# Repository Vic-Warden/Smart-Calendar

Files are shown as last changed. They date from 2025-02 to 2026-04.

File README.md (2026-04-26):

# Field Command: Pattern Cuckoo

An IoT smart calendar system built around an **ESP32** microcontroller with a Warhammer 40K aesthetic. The device retrieves appointments from a web API, displays them on an LCD, plays audio cues via a DFPlayer Mini, and adapts to ambient light. The web interface features a static landing page and a Svelte SPA.

---

## Stack

| Layer | Technology |
|---|---|
| Embedded | ESP32, PIR sensor, LDR, servo, DFPlayer Mini, I2C LCD, TM1637 |
| Backend | PHP, MariaDB (MySQL) |
| Frontend | HTML, Tailwind CSS, Three.js, Svelte + Vite |
| Infrastructure | Docker (Nginx, PHP-FPM, MariaDB, phpMyAdmin, tunnel) |

---

## Requirements

- Docker & Docker Compose
- A `.env` file at the project root (see below)

---

## Setup

1. Create a `.env` file:

```env
WEBSERVER_PORT=80
MYSQL_PORT=3306
MYSQL_ROOT_PASSWORD=your_password
HVA_USERNAME=your_username
```

2. Start the stack:

```bash
docker-compose up -d
```

| Service | URL |
|---|---|
| Web app | http://localhost/ |
| Dashboard | http://localhost/dashboard |
| phpMyAdmin | http://localhost/phpmyadmin |

---

## Project Structure

```
├── docs/          # Portfolio documentation (MkDocs)
├── embedded/      # ESP32 source code (.ino)
├── web/           # PHP, HTML, CSS, JS, assets
├── omnissiah-info/# Svelte SPA (Vite)
├── docker/        # Docker images & config
└── docker-compose.yml
```

---

## Database

| Parameter | Value |
|---|---|
| Host (from PHP) | `mariadb` |
| Host (from host) | `localhost` |
| Port | `3306` |
| Username | `root` |
| Password | See `.env` |

> Create the database manually via phpMyAdmin or MySQL CLI before first use.

---

## Communication Overview

| Source | Destination | Protocol | Port |
|---|---|---|---|
| ESP32 | PHP API | HTTP | 80 |
| ESP32 | NTP Pool | UDP | 123 |
| Mobile/Browser | Nginx | HTTPS | 443 |
| Nginx | PHP-FPM | FastCGI | 9000 |
| PHP | MariaDB | MySQL | 3306 |
| Vite Dev Server | Browser | WebSocket | 5173 |

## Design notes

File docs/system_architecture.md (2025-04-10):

# System Architecture

This page describes the system architecture of the full project, including software, hardware, and their communication. It provides a clear overview of all components within the existing Docker environment.  

This document is regularly updated to reflect the current state of the project.

---

## Introduction  

This document outlines the system architecture of my project, Field Command: Pattern Cuckoo, presenting a structured overview of its components, including software, databases, and network elements. It explains how these components interact with each other.  
The described architecture includes all elements currently present in the Docker environment.  
Its primary purpose is to serve as a reference for understanding the system.

---

## Legend  

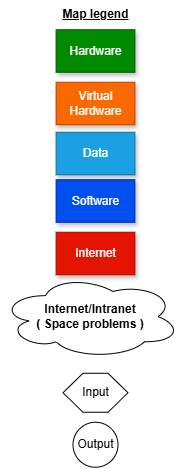
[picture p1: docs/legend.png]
  

---

## SAD#01, SAD#02, and SAD#03  

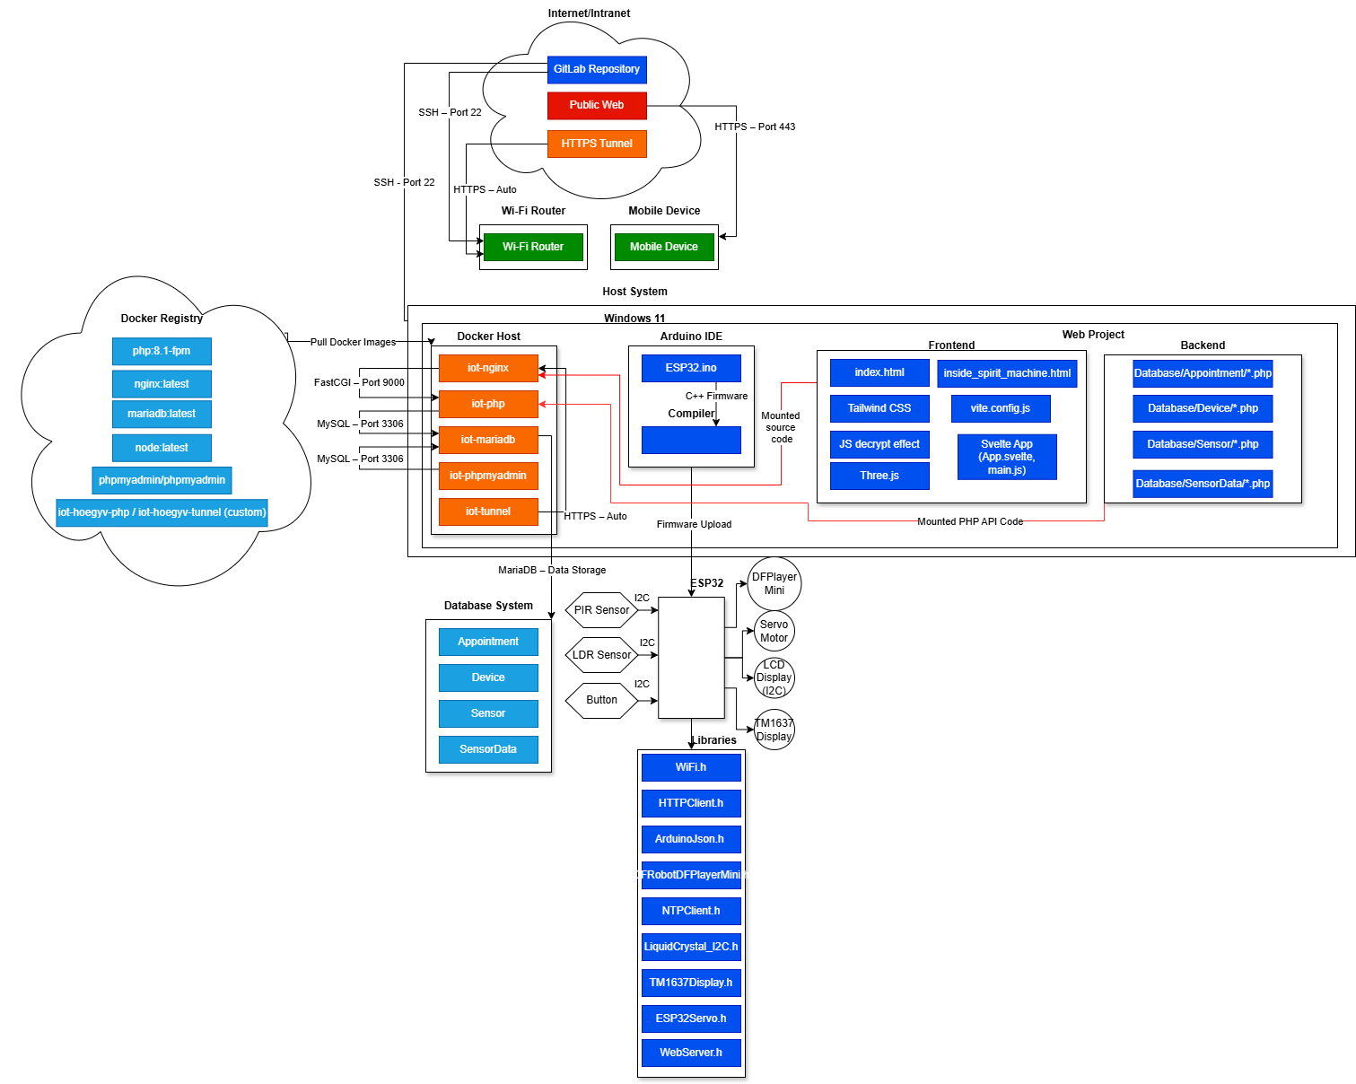
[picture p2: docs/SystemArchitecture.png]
  

---

## SAD#04  

| Source | Destination | Protocol | Port | Description |
|---|---|---|---|---|
| ESP32 | PHP API | HTTP | 80 | Retrieves + sends sensor data |
| ESP32 | NTP Pool | UDP | 123  | Time synchronization |
| ESP32 | Internal Web Server| HTTP | 80 | Testing / character switching |
| Mobile Device  | iot-nginx | HTTPS | 443  | User interface |
| iot-nginx | iot-php | FastCGI  | 9000 | API Proxy |
| iot-php | iot-mariadb | MySQL | 3306 | SQL Queries |
| phpmyadmin | iot-mariadb | MySQL | 3306 | DB Administration |
| Vite DevServer | Web Browser | WebSocket| 5173 | Live reload / frontend development |
| iot-tunnel | Internet | HTTPS | auto | Public exposure of the project |
| Host | GitLab | SSH | 22 | Code Push/Pull |

---

## SAD#05  

Menu 

---

## SAD#06  

### Hardware Components  

- **ESP32**  
- **Sensors**: PIR (motion), LDR (light), button  
- **Actuators**: Servo motor, DFPlayer Mini (audio)  
- **I2C LCD Display (16x2)**  
- **7-segment TM1637 display**  

**ESP32 Software**  

**Libraries Used**  

| Library | Role |
|---|---|
| WiFi.h | Connects ESP32 to Wi-Fi network |
| HTTPClient.h | HTTP communication with PHP APIs |
| ArduinoJson.h | Processes JSON data sent/received from the API |
| DFRobotDFPlayerMini.h | Controls DFPlayer module for audio playback |
| NTPClient.h + WiFiUdp.h| Time synchronization via NTP protocol |
| LiquidCrystal_I2C.h | Manages LCD display (text, system status) |
| TM1637Display.h | Displays time on 7-segment display |
| ESP32Servo.h | Smooth servo motor control |
| WebServer.h | Built-in HTTP server (port 80) for local commands (e.g., switching) |

**Main Functions**  

- Retrieves appointments via API and displays them on the LCD  
- Sends sensor data to the database via HTTP  
- Plays sounds via DFPlayer based on events or time  
- Automatically switches to night mode based on ambient light  

---

## SAD#07  

## Static Frontend (HTML Pages) 

- index.html, inside_spirit_machine.html  
- CSS: Tailwind  
- JS: Interactions, decrypt effect  
- Three.js + STLLoader for 3D models  

## Dynamic Frontend (Svelte SPA)  

- App.svelte, main.js (Svelte)  
- vite.config.js (dev server)  
- style.css, index.html (entry point)  
- DevServer: Vite (port 5173)  

**Backend**  

**REST APIs located in /web/Database/**  

**/Connection/**

- database_connection.php

**/Appointment/** 

- insert_appointment.php  
- update_appointment.php  
- delete_appointment.php 
- recover_appointment.php

**/Device/**  

- insert_device.php  
- delete_device.php  
- recover_device.php 

**/Sensor/**  

- insert_sensor.php  
- delete_sensor.php
- recover_sensor.php  

**/SensorData/**  

- insert_sensor_data.php
- recover_sensor_data.php  

---

## SAD#08  

- Container: iot-mariadb  
- Databases: iot, mysql, performance_schema  
- Tables: Appointment, Device, Sensor, SensorData  

---

## SAD#09  

- iot-hoegyv-php, iot-hoegyv-tunnel (custom images)  
- nginx:latest, mariadb:latest, phpmyadmin/phpmyadmin  

---

## SAD#10  

Containers running in the iot_default network:  
- iot-nginx: Web server (port 80)  
- iot-php: PHP-FPM backend  
- iot-mariadb: MariaDB database (port 3306)  
- iot-phpmyadmin: DB admin interface  
- iot-tunnel: SSH/HTTP tunnel for public exposure  

---

## SAD#11  

- Personal computer ASUS ROG Strix
- Operating system Windows 11
- Installed tools: Docker Engine, Git, IDE, browser  

---

## SAD#12  

- Android  
- Mobile OS + Chrome/Safari browser  
- Frontend interface access via HTTPS  

---

## SAD#13  

- Wi-Fi box or router  
- Connects all devices to the local network + Internet  

---

## SAD#14  

- Remote GitLab  
- .gitlab-ci.yml, .gitmodules  
- Uses SSH for push/pull  

---

## SAD#15  

- GitLab via HTTPS/SSH (port 22)  
- Public web access via iot-nginx  
- Tunnel via iot-tunnel  

---

## SAD#16  

- Container: iot-tunnel  
- Image: iot-hoegyv-tunnel  
- Public project exposure via HTTP/HTTPS tunnel  

---

**Last updated: April 7, 2025**

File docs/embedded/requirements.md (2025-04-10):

# 📜 Requirements

To build your embedded device, you need to have a clear idea of the requirements. On this page, you can describe the requirements of your embedded device. This includes the requirements from DLO, but also your own requirements.

Add some images! 😉

| Requirement ID# | Requirement | MoSCoW | Compliant |
|---|---|---|---|
| EMBRQ#01 | The embedded device acts as a client and sends measured sensor data to the application backend over http or https. | MUST | YES |
| EMBRQ#02 | The embedded device also acts as a server and receives status messages from the application backend over http or https. | MUST | YES |
| EMBRQ#03 | The embedded device contains at least two types of input sensors (e.g. LDR, buttons, joystick, capacitive touch, etc.). | MUST | YES |
| EMBRQ#04 | The embedded device contains at least two types of visual and/or sensory outputs (e.g. LED, LED Matrix, 7-segment display, motor, servo, etc.). | MUST | YES |
| EMBRQ#05 | The embedded device uses the WifiManager for configuration of SSID and password (PWD) for connecting to the network. | MUST | YES |

## EMBRQ#01

When a sensor (button, PIR or LDR) is triggered, it sends its data via a POST request, thanks to the HTTPClient library.
The API URL is defined in SENSOR_API_URL, and the sendSensorData function sends to the backend as long as WiFi is connected.

```c++

#include <WiFiManager.h>
#include <HTTPClient.h>

// The rest of the includes...

const char* SENSOR_API_URL = "http://100.74.252.69/Database/SensorData/insert_sensor_data.php";
const int DEVICE_ID = 1;

// The rest of the constants...

// Sends sensor data to the API server
 void sendSensorData(int sensor_id, float value) 
 {
   // Only send if WiFi is connected
   if (WiFi.status() != WL_CONNECTED) return;
 
   HTTPClient http;
   http.begin(SENSOR_API_URL);
   
   // Format POST data with all sensor values
   String postData = "device_id=" + String(DEVICE_ID) +
                    "&time_stamp=" + getCurrentTime() +
                    "&sensor_id_1=1&value_1=" + (sensor_id == BUTTON_SENSOR_ID ? String(value) : "0.0") +
                    "&sensor_id_2=2&value_2=" + (sensor_id == PIR_SENSOR_ID ? String(value) : "0.0") +
                    "&sensor_id_3=3&value_3=" + (sensor_id == LDR_SENSOR_ID ? String(value) : "0.0");
   
   http.POST(postData);
   http.end();
 }

// The rest of the functions...
```

## EMBRQ#02

I've defined several endpoints accessible via GET requests:

/ : returns a status message.

/appointments: returns appointments in JSON format.

/switch_character : changes character and triggers the voice of the selected character.

/play_random : plays a random sound.

The server is started in setupServer, enabling the backend to send instructions and receive data.

```c++

#include <WebServer.h>

// The rest of the includes...

WebServer server(80);
const char* SERVER_ROOT_RESPONSE = "Smart Calendar is online!";
const char* CONTENT_TYPE_TEXT = "text/plain";
const char* CONTENT_TYPE_JSON = "application/json";
const int HTTP_OK_CODE = 200;
const int HTTP_SERVICE_UNAVAILABLE_CODE = 503;

// The rest of the constants...

// Sets up the web server with all required endpoints
 void setupServer() 
 {
   // Root endpoint simple status response
   server.on("/", HTTP_GET, []() 
   {
     server.send(HTTP_OK_CODE, CONTENT_TYPE_TEXT, SERVER_ROOT_RESPONSE);
   });
 
   // Appointments endpoint returns current appointments as JSON
   server.on("/appointments", HTTP_GET, []() 
   {
     String json;
     serializeJson(appointments, json);
     server.send(HTTP_OK_CODE, CONTENT_TYPE_JSON, json);
   });
 
   // Character switch endpoint cycles to next character mode
   server.on("/switch_character", HTTP_GET, []() 
   {
     currentCharacter = static_cast<CharacterMode>((currentCharacter + 1) % CHARACTER_MODE_COUNT);
     String currentCharacterName = currentCharacterNames[currentCharacter];
 
     // Update display and play sound (if not in night mode)
     updateDisplay(LCD_MSG_SWITCHED, currentCharacterName, SHOWING_CHARACTER_NOTIFICATION);
     if (dfPlayerInitialized && !nightMode) 
     {
       switch (currentCharacter) 
       {
         case COMMISSAR: dfPlayer.play(COMMISSAR_TRACK); break;
         case LEMAN_RUSS: dfPlayer.play(LEMAN_RUSS_TRACK); break;
         case BANEBLADE: dfPlayer.play(BANEBLADE_TRACK); break;
       }
     }
 
     // Set notification timer
     showingCharacterNotification = true;
     characterNotificationStart = millis();
 
     // Return success response
     server.send(HTTP_OK_CODE, CONTENT_TYPE_TEXT, SERVER_SWITCH_RESPONSE + currentCharacterName);
   });
 
   // Play random endpoint plays random voice line for current character
   server.on("/play_random", HTTP_GET, []() 
   {
     if (dfPlayerInitialized && !nightMode) 
     {
       // Play random sound based on current character
       switch (currentCharacter) 
       {
         case COMMISSAR:
           playRandomSound(COMMISSAR_ACTIVE_TRACKS, sizeof(COMMISSAR_ACTIVE_TRACKS)/sizeof(int));
           break;
         case LEMAN_RUSS:
           playRandomSound(LEMAN_RUSS_ACTIVE_TRACKS, sizeof(LEMAN_RUSS_ACTIVE_TRACKS)/sizeof(int));
           break;
         case BANEBLADE:
           playRandomSound(BANEBLADE_ACTIVE_TRACKS, sizeof(BANEBLADE_ACTIVE_TRACKS)/sizeof(int));
           break;
       }

       server.send(HTTP_OK_CODE, CONTENT_TYPE_TEXT, "Random voice line played.");
     } 
     
     else 
     {
       // Return error if conditions not met
       server.send(HTTP_SERVICE_UNAVAILABLE_CODE, CONTENT_TYPE_TEXT, "Night mode active or DFPlayer unavailable.");
     }
   });
 
   server.begin();
   Serial.println(SERIAL_MSG_HTTP_STARTED);
 }

// The rest of the functions...
```

## EMBRQ#03

I use 3 inputs

A push-button (pin 14) used to change character.

A PIR sensor (pin 35) to detect movement.

An LDR sensor (pin 34) which measures ambient brightness.

All these sensors are read by the handleSensors function, and each change triggers an action ( sending data, sound ). 

```c++

#include <Wire.h>     
#include <ArduinoJson.h> 

// The rest of the includes...

 // Input 
 const int BUTTON_PIN = 14;             
 const int PIR_PIN = 35;                
 const int LDR_PIN = 34;

  enum SensorIds 
 {
   BUTTON_SENSOR_ID = 1, 
   PIR_SENSOR_ID = 2,        
   LDR_SENSOR_ID = 3           
 };

// The rest of the constants...

// Checks and handles sensor inputs
 void handleSensors(unsigned long currentMillis) 
 {
   // Only check sensors at defined interval
   if (currentMillis - lastSensorCheck >= SENSOR_CHECK_INTERVAL_MS) 
   {
     lastSensorCheck = currentMillis;
     
     // Read all sensor values
     int buttonState = digitalRead(BUTTON_PIN);
     int pirState = digitalRead(PIR_PIN);
     int ldrValue = analogRead(LDR_PIN);
     static bool wasInNightMode = nightMode;
     
     // Check for night mode transition
     bool newNightMode = (ldrValue < NIGHT_MODE_ENTER_THRESHOLD);
     if (newNightMode != nightMode) 
     {
       nightMode = newNightMode;
 
       // Play appropriate day/night sound if DFPlayer is ready
       if (dfPlayerInitialized) 
       {
         dfPlayer.play(nightMode ? DARK_TRACK : LIGHT_TRACK);
       }
 
       wasInNightMode = nightMode;
       sendSensorData(LDR_SENSOR_ID, ldrValue);
     }
 
     // Check for button press (with debouncing)
     if (buttonState == LOW && lastButtonState == HIGH && (currentMillis - lastButtonPress) >= BUTTON_DEBOUNCE_TIME_MS) 
     {
       sendSensorData(BUTTON_SENSOR_ID, VALUE_TRUE);
       
       // Cycle to next character mode
       currentCharacter = static_cast<CharacterMode>((currentCharacter + 1) % CHARACTER_MODE_COUNT);
       String currentCharacterName = currentCharacterNames[currentCharacter];
       
       // Show character switch notification
       updateDisplay(LCD_MSG_SWITCHED, currentCharacterName, SHOWING_CHARACTER_NOTIFICATION);
       
       // Play character-specific sound if not in night mode
       if (dfPlayerInitialized && !nightMode) 
       {
         switch(currentCharacter) 
         {
            case COMMISSAR: dfPlayer.play(COMMISSAR_TRACK); break;
            case LEMAN_RUSS: dfPlayer.play(LEMAN_RUSS_TRACK); break;
            case BANEBLADE: dfPlayer.play(BANEBLADE_TRACK); break;
         }
       }
       
       // Set notification display timer
       showingCharacterNotification = true;
       characterNotificationStart = currentMillis;
       lastButtonPress = currentMillis;
     }
 
     // Check for motion detection (with cooldown period )
     if (pirState == HIGH && lastPIRState == LOW && !pirLocked) 
     {
       sendSensorData(PIR_SENSOR_ID, VALUE_TRUE);
       
       // Play random motion sound if not in night mode
       if (dfPlayerInitialized && !nightMode) 
       {
         playRandomSound(PIR_TRACKS, sizeof(PIR_TRACKS)/sizeof(int));
       }
 
       // Start cooldown period
       lastPIRTime = currentMillis;
       pirLocked = true;
     }
 
     // Reset PIR lock after cooldown period
     if (pirLocked && currentMillis - lastPIRTime >= PIR_INTERVAL_MS) 
     {
       pirLocked = false;
     }
 
     // Update previous sensor states
     lastButtonState = buttonState;
     lastPIRState = pirState;
     lastLDRValue = ldrValue;
   }
 }

 // The rest of the functions...
```

## EMBRQ#04

I use 4 outputs

LCD display (I2C): displays appointments and system messages via updateDisplay

7-segment display: displays time in real time via update7SegmentDisplay.

DFPlayer audio module: plays sounds in response to events (sensors, changes) via playRandomSound

Servomotor: performs a movement every hour via handleHourlyServo

```c++

#include <LiquidCrystal_I2C.h>   
#include <TM1637Display.h>       
#include <DFRobotDFPlayerMini.h> 
#include <ESP32Servo.h>       

// The rest of the includes...

// LCD
 const int LCD_I2C_ADDRESS = 0x27;     
 const int LCD_COLUMNS = 16;            
 const int LCD_ROWS = 2;               
 const int LCD_SDA_PIN = 21;           
 const int LCD_SCL_PIN = 22; 
 const int LCD_START_COL = 0;
 const int LCD_FIRST_LINE = 0;
 const int LCD_SECOND_LINE = 1;
           
// 7 segment 
 const int DISPLAY_CLK_PIN = 18;        
 const int DISPLAY_DIO_PIN = 19;         
 const uint8_t DISPLAY_BRIGHTNESS = 0x0a;
 const uint8_t DISPLAY_COLON_MASK = 0b01000000;
 const int DISPLAY_ERROR_CODE = 9999;   
 const int DISPLAY_DEFAULT_CODE = 8888;  
 const int DISPLAY_TIME_SCALING = 100;
 
 // DFPlayer Mini 
 const int DFPLAYER_RX_PIN = 16;         
 const int DFPLAYER_TX_PIN = 17;         
 const int DFPLAYER_VOLUME = 15;          
 const int DFPLAYER_MIN_PLAY_INTERVAL_MS = 100;
 const int DFPLAYER_BAUD = 9600;        
 
 // Servo Motor 
 const int SERVO_PIN = 27;               
 const int SERVO_MIN_POSITION = 90;     
 const int SERVO_MAX_POSITION = 180;     
 const int SERVO_SPEED = 1;             
 const unsigned long SERVO_UPDATE_INTERVAL_MS = 20;
 const unsigned long SERVO_TEST_PAUSE_MS = 1000;    
 const unsigned long HOURLY_SERVO_DURATION_MS = 60000; 
 const int SERVO_PULSE_MIN = 500;      
 const int SERVO_PULSE_MAX = 2500;

 // The rest of the constants...

 // Updates the LCD display with new content if it has changed
 void updateDisplay(String line1, String line2, DisplayState newState) 
 {
   static String lastLine1 = "";      // Previously displayed first line
   static String lastLine2 = "";      // Previously displayed second line
   static DisplayState lastState = SHOWING_INITIALIZATION; // Previous state
 
   // Only update display if content or state has changed
   if (newState != lastState || line1 != lastLine1 || line2 != lastLine2) 
   {
     lcd.clear();  // Clear the display before showing new content
     
     // Display first line
     lcd.setCursor(LCD_START_COL, LCD_FIRST_LINE);
     lcd.print(line1.substring(0, LCD_COLUMNS));
 
     // Display second line
     lcd.setCursor(LCD_START_COL, LCD_SECOND_LINE);
     lcd.print(line2.substring(0, LCD_COLUMNS));
 
     // Update tracking variables
     lastLine1 = line1;
     lastLine2 = line2;
     lastState = newState;
     currentDisplayState = newState;
   }
 }

 // Updates the 7-segment display with current time
 void update7SegmentDisplay() 
 {
   // Show error code if time hasn't been initialized
   if (!timeInitialized) 
   {
     display.showNumberDec(DISPLAY_ERROR_CODE);
     return;
   }
   
   // Update time from NTP server and display it
   timeClient.update();
   int hour = timeClient.getHours() + 1; // Adjust for timezone
   // Handle 24-hour rollover
   if (hour >= HOURS_PER_DAY) hour -= HOURS_PER_DAY;
   int minute = timeClient.getMinutes();
   // Display time with colon (e.g., 12:34)
   int timeDisplay = hour * DISPLAY_TIME_SCALING + minute;
   display.showNumberDecEx(timeDisplay, DISPLAY_COLON_MASK, true);
 }

 // Plays a random sound from the specified track list
 void playRandomSound(const int tracks[], int count) 
 {
   // Don't play if DFPlayer not ready, no tracks, or in night mode
   if (!dfPlayerInitialized || count <= 0 || nightMode) return;
   
   static unsigned long lastPlayTime = 0; // Track last play time for debouncing
   unsigned long currentMillis = millis();
   
   // Only play if minimum interval has passed
   if (currentMillis - lastPlayTime > DFPLAYER_MIN_PLAY_INTERVAL_MS) 
   {
     int randomIndex = random(0, count);
     dfPlayer.play(tracks[randomIndex]);
     lastPlayTime = currentMillis;
   }
 }

 // Handles hourly servo movement 
 void handleHourlyServo(unsigned long currentMillis) 
 {
   static int lastTriggeredHour = -1; // Track last hour servo was activated
   
   // Don't activate if time not initialized
   if (!timeInitialized) return;
   
   // Get current time
   timeClient.update();
   int currentHour = timeClient.getHours();
   int currentMinute = timeClient.getMinutes();
   
   // Trigger at top of each new hour
   if (currentMinute == 0 && currentHour != lastTriggeredHour) 
   {
     servoTargetPosition = SERVO_MIN_POSITION;
     servoMoving = true;
     Serial.println(SERIAL_MSG_SERVO_MOVING_MIN);
     lastTriggeredHour = currentHour;
     servoReturnTime = currentMillis + HOURLY_SERVO_DURATION_MS;
   }
   
   if (servoTargetPosition == SERVO_MIN_POSITION && currentMillis >= servoReturnTime) 
   {
     servoTargetPosition = SERVO_MAX_POSITION;
     servoMoving = true;
     Serial.println(SERIAL_MSG_SERVO_MOVING_MAX);
   }
 
   if (currentMillis - lastServoUpdate >= SERVO_UPDATE_INTERVAL_MS) 
   {
     if (servoCurrentPosition != servoTargetPosition) 
     {
       int direction = (servoTargetPosition > servoCurrentPosition) ? 1 : -1;
       servoCurrentPosition += direction * SERVO_SPEED;
       servoCurrentPosition = constrain(servoCurrentPosition, SERVO_MIN_POSITION, SERVO_MAX_POSITION);
       
       servo1.write(servoCurrentPosition);
       lastServoUpdate = currentMillis;
     }
     
     else if (servoMoving) 
     {
       servoMoving = false;
       Serial.println(SERIAL_MSG_SERVO_REACHED);
     }
   }
 }

// The rest of the functions...
```

## EMBRQ#05

I used the WiFiManager library, which enables the ESP32 to automatically manage the WiFi connection.

The connectToWiFi function uses wifiManager.autoConnect

If no network is known, the device creates an access point named “SmartCalendarAP” to allow the user to enter the SSID and password via a web interface.

Once connected, the system continues its configuration.

```c++

#include <WiFiManager.h>

// The rest of the includes...

const char* WIFI_AP_NAME = "SmartCalendarAP"; 
const char* LCD_MSG_WIFI_START = "Starting WiFi";
const char* LCD_MSG_WIFI_FAIL = "WiFi Failed";
const char* LCD_MSG_WIFI_CONNECTED = "WiFi Connected";

 // The rest of the constants...

// Connects to WiFi using WiFiManager
 void connectToWiFi() 
 {
   WiFiManager wifiManager;
   updateDisplay(LCD_MSG_WIFI_START, "", SHOWING_INITIALIZATION);
   
   // Attempt to connect to WiFi or start configuration AP
   if (!wifiManager.autoConnect(WIFI_AP_NAME)) 
   {
     // Connection failed show message and restart
     updateDisplay(LCD_MSG_WIFI_FAIL, LCD_MSG_RESTARTING, SHOWING_INITIALIZATION);
     delay(DELAY_WIFI_FAIL_MS);
     ESP.restart();
     delay(DELAY_AFTER_RESTART_MS);
   }
   
   // Connection successful proceed to time sync
   updateDisplay(LCD_MSG_WIFI_CONNECTED, LCD_MSG_SYNCING, SHOWING_INITIALIZATION);
   initializeTime();
 }

// The rest of the functions...
```

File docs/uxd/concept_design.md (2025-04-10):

# Concept & Design

Write here your own content!

## Project Goal 

The main goal is to offer Warhammer 40,000 fans an interactive way to manage their calendar. This is done through a personalized smart calendar that blends physical and digital interaction, allowing users to add and manage appointments via a web interface. Each interaction is enhanced by audio and visual feedback from the Warhammer universe. The final goal is to have a fully functional prototype by the end of the ten weeks.

## Target User

- **Target audience:** Fans of the Warhammer 40,000 universe (estimated community between 30 and 50 million people).
- **Usage context:** Users want to add tasks to their calendar, but the process is repetitive and annoying.
- **Problem:** Adding tasks to the calendar is monotonous.
- **Solution:** A Warhammer-themed smart calendar, responsive to user presence, with iconic lighting effects and sounds.

## User Stories

US01: As a Warhammer fan, I want to hear iconic voices when I add an appointment so I can have an immersive experience.

US02: As a user, I want to quickly add appointments via a web interface to save time.

US03: As a curious user, I want to explore an original calendar interface so that my experience is new and engaging.

US04: As a passionate user, I want to choose a voice for each appointment to personalize it.

US05: As a user, I want the calendar to react to my presence so that the object seems alive.

## Requirements

PR01: The calendar must detect user presence and light up the eyes of the Warhammer emblem.

PR02: The interface must allow adding or modifying appointments in less than 20 seconds.

PR03: Each interaction must trigger a sound from Warhammer games.

PR04: The user must be able to select a custom voice for each appointment.

PR05: The device must integrate an LCD screen and a PIR sensor.

## Digital Manufacturing & Materials

- **Software used :** Tinkercad  

Chosen for its simplicity

- **Material used :** **PLA** 

  PLA was chosen for its ease of printing, low warping, and aesthetic finish, ideal for a decorative object like this smart calendar.

- **Why this method ?**  

Tinkercad and PLA allow for fast prototyping, precise part design, and compatibility with 3D printers

**Inspiration & Visual References**

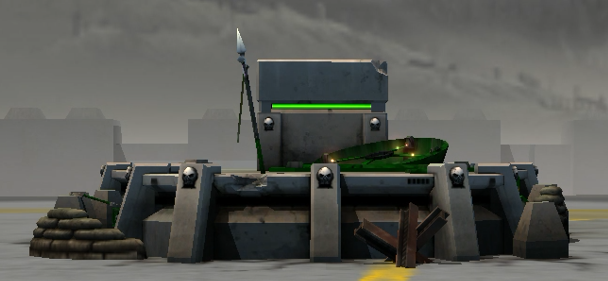
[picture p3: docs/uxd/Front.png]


Front view

---

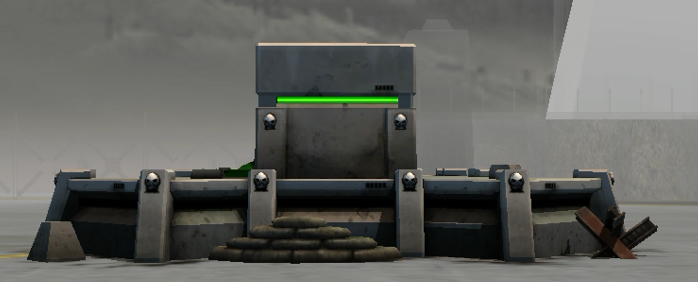
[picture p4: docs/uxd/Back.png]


Back view

---

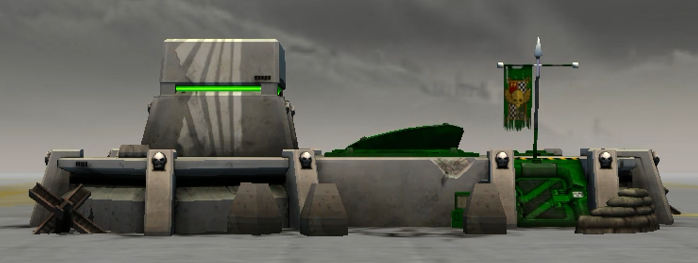
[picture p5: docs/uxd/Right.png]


Right side

---

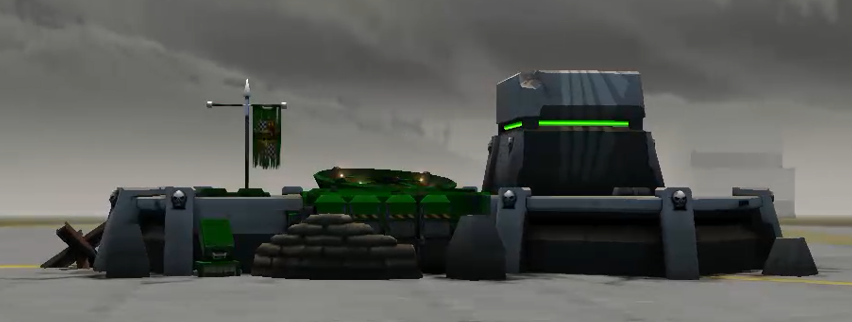
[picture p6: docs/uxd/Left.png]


Left side

---

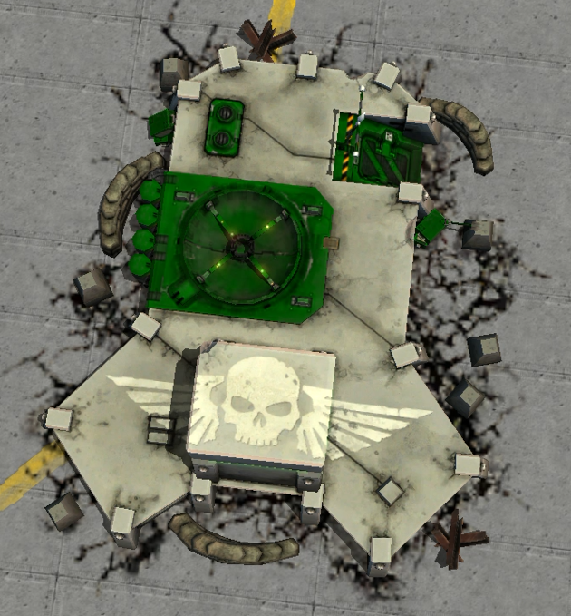
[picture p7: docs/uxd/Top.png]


Top view

---

**3D Prototyping via Tinkercad**

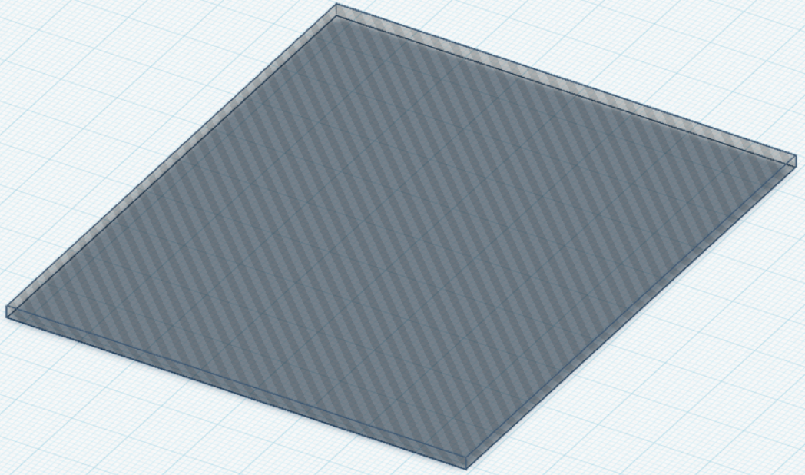
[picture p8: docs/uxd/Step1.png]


**Step 1:** Creation of a first rectangle to serve as a base

Dimensions:  86.00 mm × 74.00 mm 

---

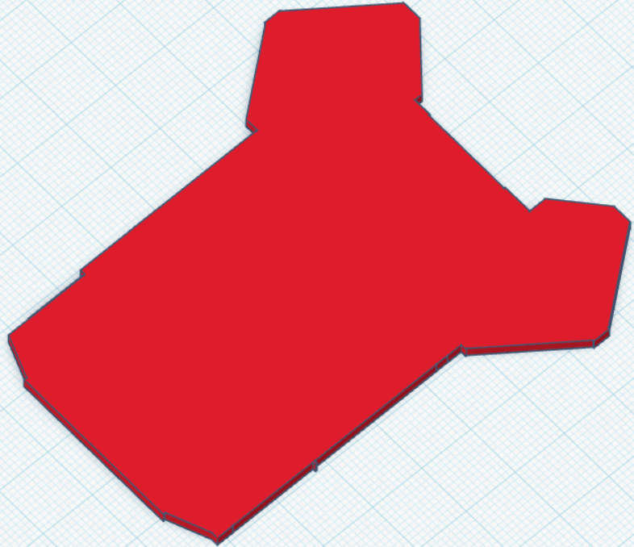
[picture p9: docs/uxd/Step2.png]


[Download Step 2](https://gitlab.fdmci.hva.nl/IoT/2024-2025-semester-2/individual-project/buudiizaaduu29/-/blob/main/docs/uxd/3D%20Model/Step2.stl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)

**Step 2:** Adjustment of the rectangle to surround the base

Dimensions:  86.00 mm × 74.00 mm × 2.00 mm

---

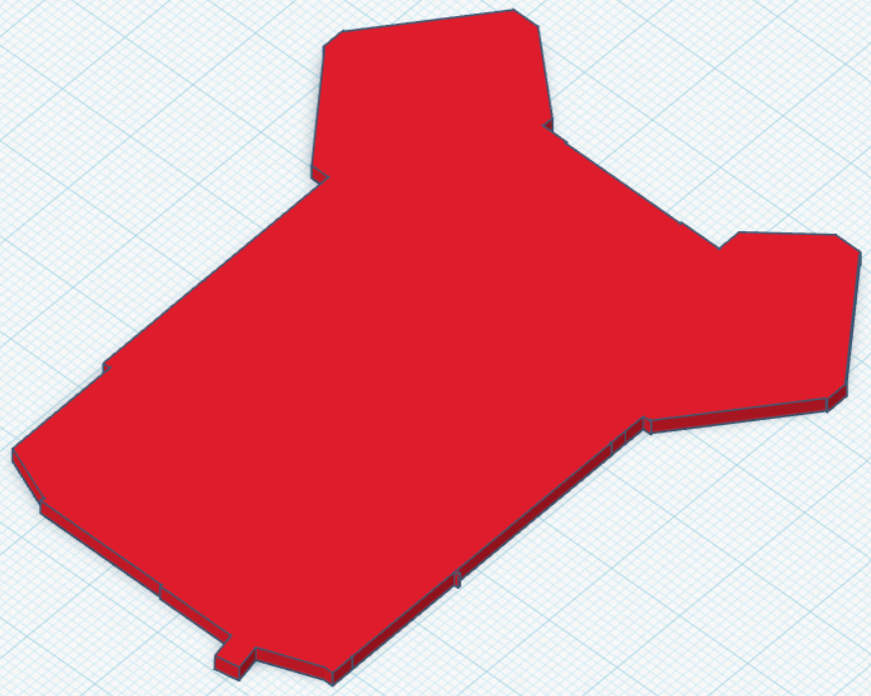
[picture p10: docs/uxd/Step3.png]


**Step 3:** Cutting the rectangle to create a pillar

---

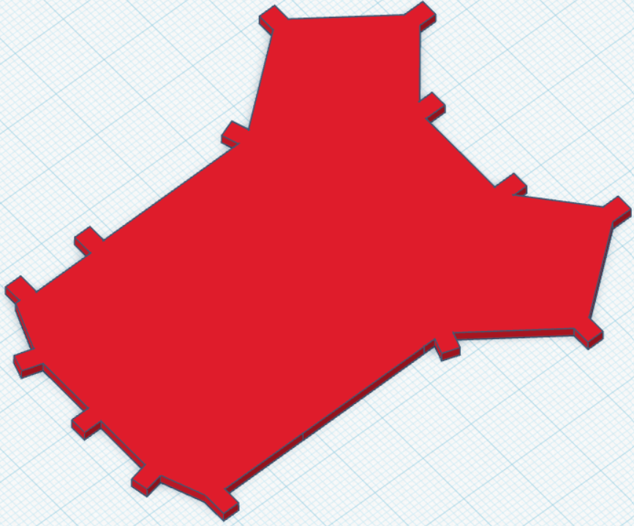
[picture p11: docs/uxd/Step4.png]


[Download Step 4](https://gitlab.fdmci.hva.nl/IoT/2024-2025-semester-2/individual-project/buudiizaaduu29/-/blob/main/docs/uxd/3D%20Model/Step4.stl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)

**Step 4:** Repeat the process for several pillars

---

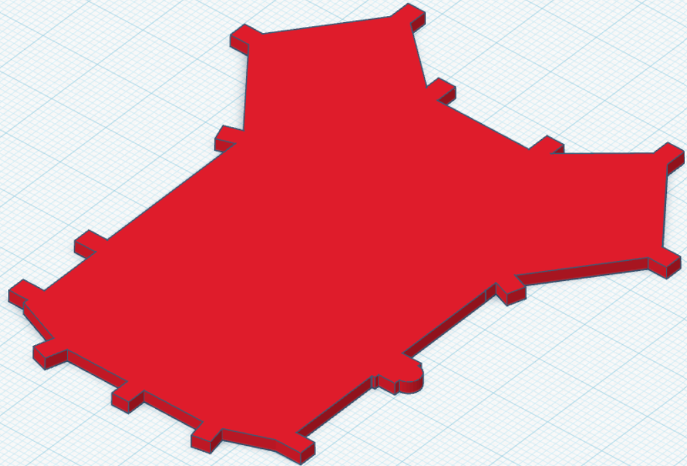
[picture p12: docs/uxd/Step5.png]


**Step 5:** Attempt to create energy generators

---

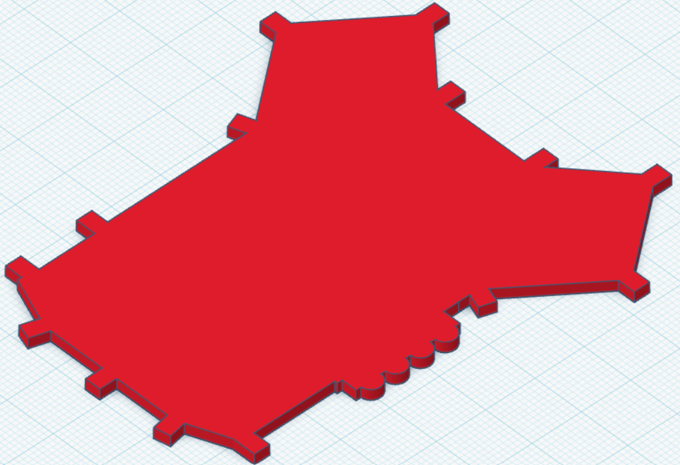
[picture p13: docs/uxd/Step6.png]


[Download Step 6](https://gitlab.fdmci.hva.nl/IoT/2024-2025-semester-2/individual-project/buudiizaaduu29/-/blob/main/docs/uxd/3D%20Model/Step6.stl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)

**Step 6:** Duplicate the generators

---

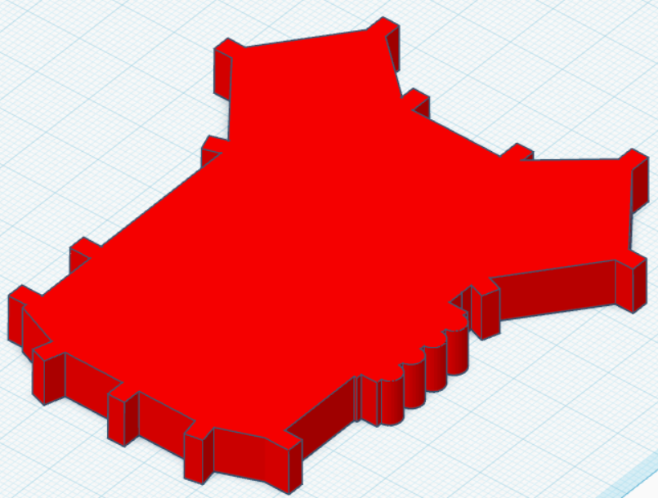
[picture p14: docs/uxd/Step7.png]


**Step 7:** Enlargement of the base

Dimensions 93.48 mm × 80.44 mm × 8.49 mm

---

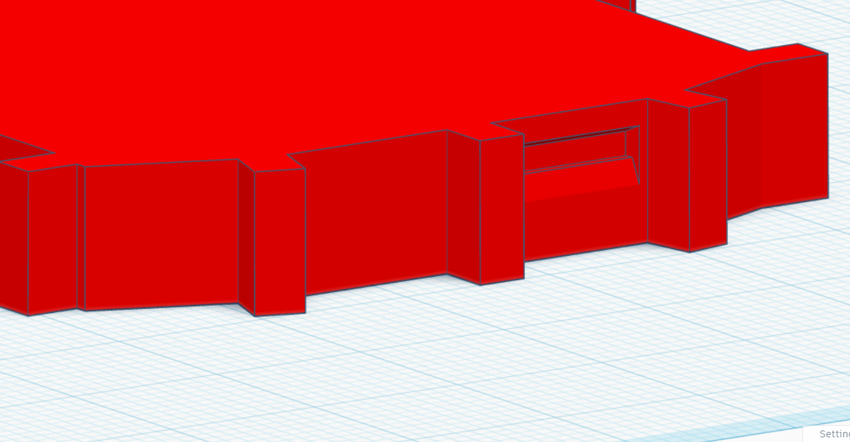
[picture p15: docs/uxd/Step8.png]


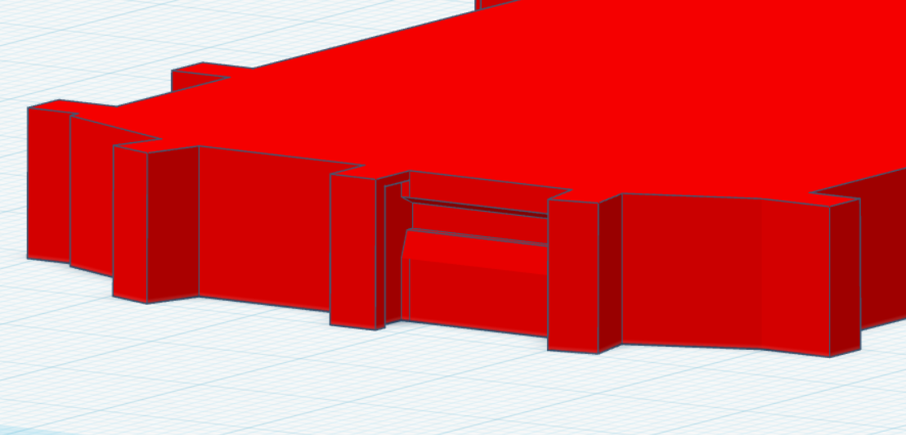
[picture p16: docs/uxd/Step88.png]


[Download Step 8](https://gitlab.fdmci.hva.nl/IoT/2024-2025-semester-2/individual-project/buudiizaaduu29/-/blob/main/docs/uxd/3D%20Model/Step8.stl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)

**Step 8:** Installation of the observation post

---

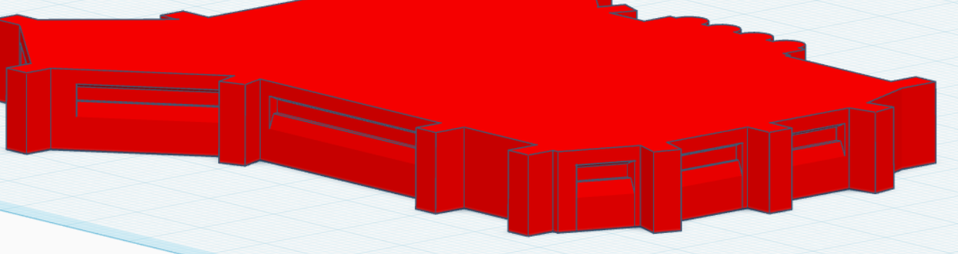
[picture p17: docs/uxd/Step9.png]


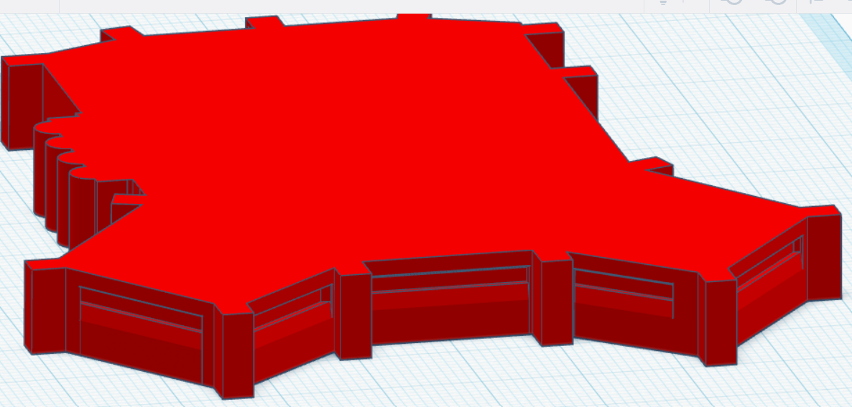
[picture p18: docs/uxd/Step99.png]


[Download Step 9](https://gitlab.fdmci.hva.nl/IoT/2024-2025-semester-2/individual-project/buudiizaaduu29/-/blob/main/docs/uxd/3D%20Model/Step9.stl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)

**Step 9:** Duplication of the observation post

---

**Improvement & Correction**

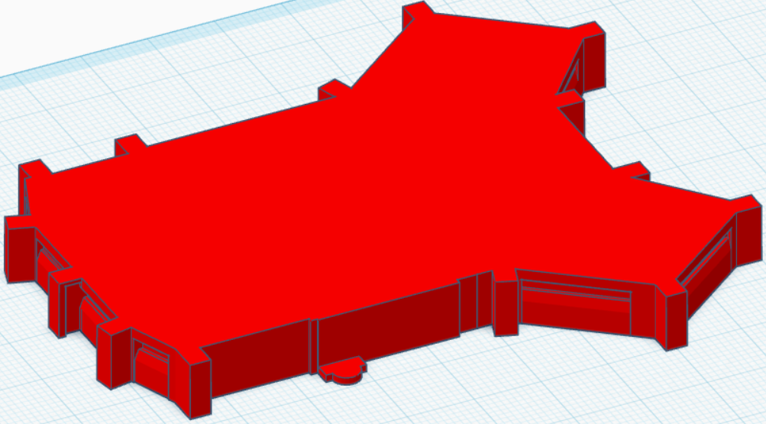
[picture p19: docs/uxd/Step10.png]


[Download Step 10](https://gitlab.fdmci.hva.nl/IoT/2024-2025-semester-2/individual-project/buudiizaaduu29/-/blob/main/docs/uxd/3D%20Model/Step10.stl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)

**Step 10:** Redesign of energy generators deemed unaesthetic

---

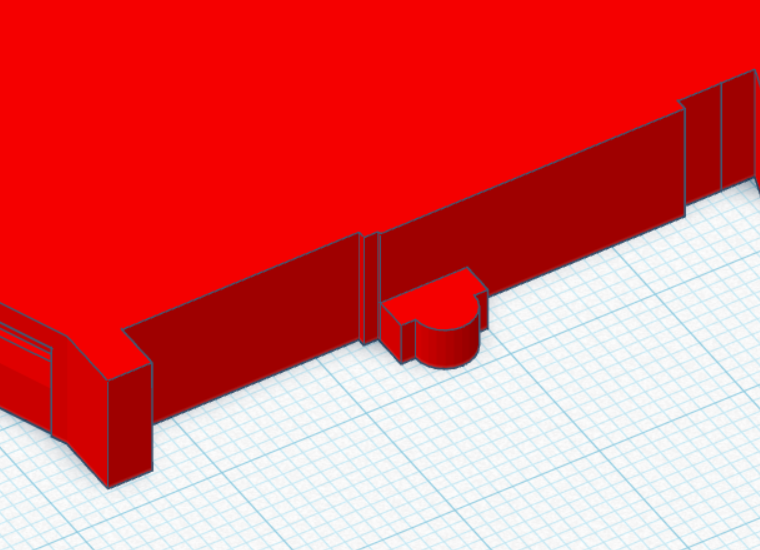
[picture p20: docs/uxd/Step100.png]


**Step 11:** Enlargement of generators

---

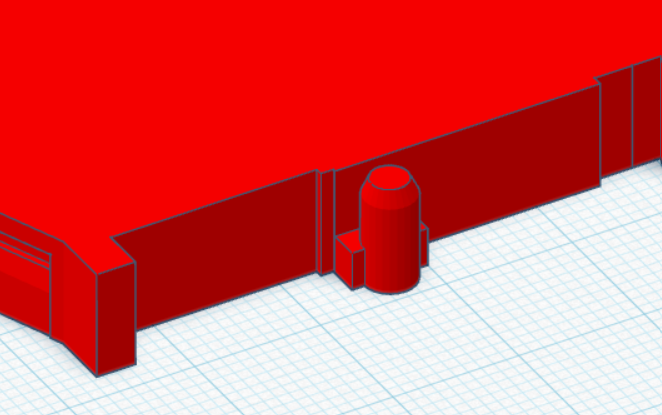
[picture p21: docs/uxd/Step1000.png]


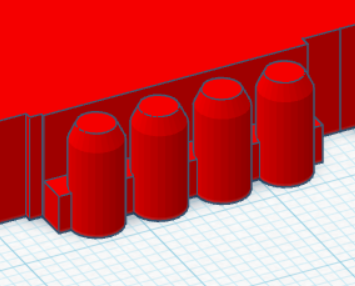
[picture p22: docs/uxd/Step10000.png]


**Step 12:** Cutting the end and duplication

---

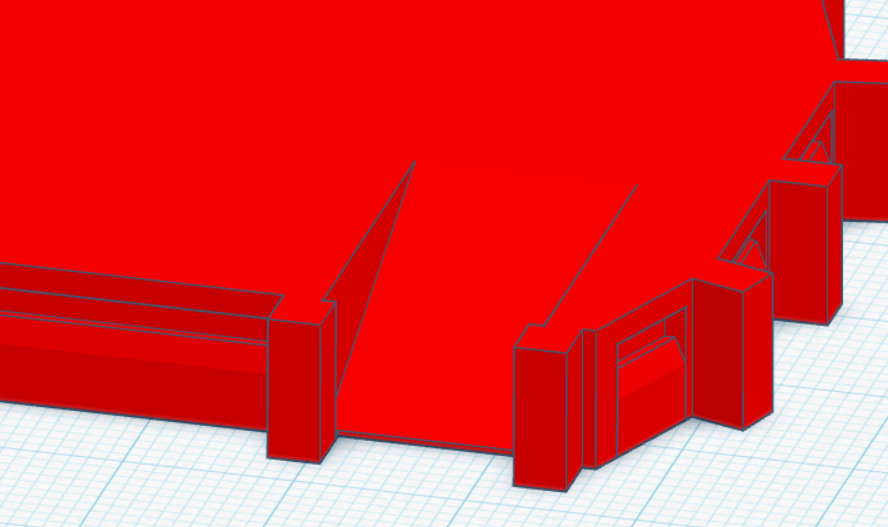
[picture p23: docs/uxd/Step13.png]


**Step 13:** Adding a door

---

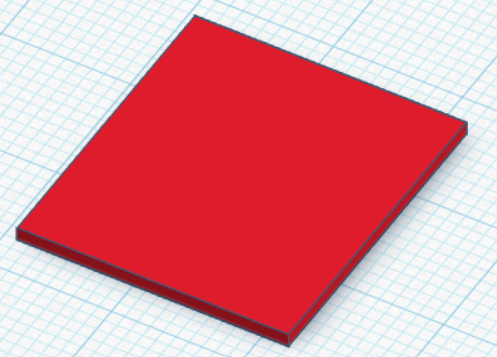
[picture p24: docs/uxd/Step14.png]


**Step 14:** Creating a rectangle for the tower

---

Menu

**Step 15:** Cutting the rectangle for a more refined shape

---

Menu

**Step 16:** Enlargement of the tower

---

Menu

**Step 17:** Adding a square on the tower and reducing the central part for an observation post look

---

Menu

[Download Step 18](https://gitlab.fdmci.hva.nl/IoT/2024-2025-semester-2/individual-project/buudiizaaduu29/-/blob/main/docs/uxd/3D%20Model/Step18.stl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)

**Step 18:** Adding the tower to the base

Dimensions: 93.48 mm × 80.44 mm × 27.40 mm

---

Menu

[Download Step 19](https://gitlab.fdmci.hva.nl/IoT/2024-2025-semester-2/individual-project/buudiizaaduu29/-/blob/main/docs/uxd/3D%20Model/Step19.stl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)

**Step 19:** Enlargement to accommodate the LCD screen and PIR sensor

Dimensions: 200.00 × 172.10 × 84.99 mm

---

Menu

**Step 20:** Attempt to make the base hollow

---

Menu

**Step 21:** Decision to divide the model into two parts: base and tower

---

**Final Export for Manufacturing**

Menu

Menu

Menu

[Download the tower](https://gitlab.fdmci.hva.nl/IoT/2024-2025-semester-2/individual-project/buudiizaaduu29/-/blob/main/docs/uxd/3D%20Model/Step222.stl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)

[Download the base](https://gitlab.fdmci.hva.nl/IoT/2024-2025-semester-2/individual-project/buudiizaaduu29/-/blob/main/docs/uxd/3D%20Model/Step2222.stl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)

**Step 22:** Finalizing the shapes and hollowing out the volumes via Meshmixer

---

**Component Integration**

Menu  

[Download final version](https://gitlab.fdmci.hva.nl/IoT/2024-2025-semester-2/individual-project/buudiizaaduu29/-/blob/main/docs/uxd/3D%20Model/Last.stl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)

**Step 23:** Drilling for components and preparation for 3D printing

Dimensions: 199.99 × 172.09 × 92.00

---

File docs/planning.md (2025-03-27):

# Planning

## Eighth week

### Thursday 27/03

- ✅ Print the base 3D models

- ✅ Technical documentation

- 🔄 Split the embedded code

- 🔄 Improve front-end with React

- 🔄 Documentation

### Wenesday 26/03

- ✅ See for prints, documentation and pick up my cuckoo clock for the 3D model

### Tuesday 25/03

- ✅ ESP32 Code

### Monday 24/03

- ✅ 3D Models

--- 

## Seventh week

### Thursday 20/03

**Create & Test**

- 🔄 The manufacturing process is logged with pictures and/or video’s as proof

### Wenesday 19/03

**Research to market**

- ✅ Introduction / context

- ✅ Research question

- ✅ Research method

### Tuesday 18/03

ESP32 Code

- ✅ Play a sound when we add, edit or delete an appointment

- ❌ Connect to the Internet using wifi manager

- 🔄 Retrieve appointments and take action accordingly

- 🔄 Send data

- 🔄 Make sensors do something once activated

### Monday 17/03

Research part

- ✅ Choose the following are to focus on

- 🔄 Introduction

- 🔄 Research method

Composants connected to the ESP32 

- ✅ 7 segments

- ✅ Button

- ✅ DF Player Mini

- ✅ LED

- ✅ Photo Resistor

- ✅ Screens ( Both )

- ✅ Servo

Programs

- ✅ DF Player with button

Database

- ✅ Add status -> appointment

- ✅ Add note & request method put -> update appointment

Website

- ✅ Changement Request method put -> update appointment

- ✅ Changement JS -> update appointment

- ✅ Changement Request method delete -> delete appointment

- ✅ Changement JS -> delete appointment

ESP32 Code

- 🔄 Almost...

---

## Sixth week

### Friday 14/03

To be done later :

- 🔄 3D model change stuff

- 🔄 Resume API reference

- 🔄 Research part to be done from Friday

### Thursday 13/03

Program working alone :

Arduino :

- ✅ Heart Bip Bip code

- ✅ DF Player mini code

- ✅ LED code

- ✅ Servo motor code

- ✅ 7 segments code

Wemos :

- ✅ Button code

- ✅ Photoresistor code

- ✅ PIR Sensor code

Program working together ( in pairs ):

- ❌ When a button is clicked, a random sound is played

- ❌ When the PIR sensor detects someone, it launches a single specific voice line

- ❌ When the photo resistance falls below 200, it launches a voice line to indicate that it is switching to silent mode

- ❌ When an appointment is received, it launches a sound

To be done later :

- 🔄 3D model change stuff

- 🔄 Resume API reference

- 🔄 Research part to be done from Friday

### Wenesday 12/03

Documentation

- ✅ System Architecture

- ✅ Requirements

- ✅ Technical documentation Embedded

- 🔄 Embedded code ( need to finish the code first, I will code tomorrow I mean in few hours )

- ✅ Technical Documentation Web

- ✅ Database

Program :

- 🔄 Wemos

- 🔄 Arduino

To be done later :

- 🔄 3D model change stuff

- 🔄 Resume API reference

- 🔄 Research part to be done from Friday

### Tuesday 11/03

Database :

- ✅ Database Schema

- ✅ ERD Schema

API :

- ✅ Insert Device

- ✅ Delete Device

- ✅ Recover Device

- ✅ Insert Sensor

- ✅ Delete Sensor

- ✅ Recover Sensor

- ✅ Instert Sensor Data

- ✅ Delete Sensor Data

- ✅ Recover Sensor Data

Program :

- ✅ Arduino control via wemos

- ✅ Control sound at the touch of a button

- 🔄 Wemos

- 🔄 Arduino

To be done later :

- 🔄 3D model change stuff

- 🔄 Resume API reference

- 🔄 Research part to be done from Friday

### Monday 10/03

Wemos Connection :

- ✅ PIR sensor

- ✅ Photoresistor

- ✅ Button

- ✅ Arduino

Arduino Connection :

- ✅ 7 segments display time

- ✅ Heartbeat

- ✅ Servo motor

- ✅ DF Player Mini

- ✅ Wemos

API :

- ✅ Connecting to an API using the wemos

- ✅ Connecting Wemos to the database

- ✅ Send data from wemos to the database 

- 🔄 Insert Sensor

- 🔄 Delete Sensor

- 🔄 Recover Sensor

- 🔄 Instert Sensor Data

- 🔄 Delete Sensor Data

- 🔄 Recover Sensor Data

Documentation :

- ✅ Frietzing

- 🔄 System Architecture

Program :

- 🔄 Wemos

- 🔄 Arduino

To be done later :

- 🔄 3D model change stuff

- 🔄 Resume API reference

- 🔄 Research part to be done from Friday

---

## Fith week

## Friday 07/03

- 🔄 PIR sensor -> Wemos 

- 🔄 DF Player Mini -> Wemos

- ✅ Connecting to an API using the wemos

- ✅ Connecting Wemos to the database

- 🔄 Send data from wemos to the database 

- 🔄 3D model change stuff

- 🔄 Resume API reference

## Thursday 06/03

- 🔄 PIR sensor -> Wemos 

- 🔄 DF Player Mini -> Wemos

- ✅ 7 segments display time -> Arduino

- ✅ Heartbeat -> Arduino

- ✅ Servo motor -> Arduino

- 🔄 Connecting to an API using the wemos

- 🔄 Connecting Wemos to the database

- 🔄 Send data from wemos to the database 

- 🔄 3D model change stuff

- 🔄 Resume API reference

## Wenesday 05/03

- ✅ Connecting to the internet with WiFi Manager

- ✅ Recover the IP Adress 

- ✅ 2 LED -> Wemos

- ✅ PIR sensor -> Wemos 

- ✅ Button -> Wemos

- ✅ Photo resistor -> Wemos

- 🔄 DF Player Mini -> Wemos

- 🔄 7 segments display time -> Arduino

- 🔄 Heartbeat -> Arduino

- 🔄 Servo motor -> Arduino

- 🔄 Connecting to an API using the wemos

- 🔄 Connecting Wemos to the database

- 🔄 Send data from wemos to the database 

- 🔄 3D model change stuff

- 🔄 Resume API reference

### Tuesday 04/03

- ✅ API when adding an appointment
- ✅ API when deleting an appointment 
- ✅ API when editing an appointment 
- ✅ API to Recover all appointments 

- ✅ API to have only the last added
- ✅ API to have only the last edited 
- ✅ API to have only the last updated 

### Monday 03/03

- ✅ Add an appointment from the website
- ✅ Delete an appointment from the website
- ✅ Edit an appointment from the website
- ✅ Recover an appointment from the database

---

## Fourth week :

### Friday 28/02
- ✅ Watch a video to learn how to connect a website to a database
- ✅ Watch a youtube video to understand wemos
- ✅ 🥳🥳 Have a database connection 🥳🥳

### Thursday 27/02

- 🔄 Watch a youtube video to understand wemos
- 🔄 Understanding where saturation comes from  
- ✅ Watch a video to learn how to connect a website to a database
- ✅ Participate at a presentation 
- ✅ Redo System Architecture to include input, output and text
- ✅ Redo Data Base with detailed why and how 
- ✅ Redo Requirements 

### Wednesday 26/02

- 🔄 Watch a youtube video to understand wemos  
- 🔄 Watch a video to learn how to connect a website to a database
- 🔄 Understanding where saturation comes from
- ✅ Redo the documentation for my Wiring Diagram
- ✅ Find a way to save space for wemos
- ✅ Add element to system architecture
- ✅ Heartbeat simulation

### Tuesday 25/02

- 🔄 Watch a youtube video to understand wemos  
- 🔄 Watch a video to learn how to connect a website to a database
- 🔄 Redo the documentation for my Wiring Diagram
- 🔄 Understanding where saturation comes from
- ✅ Operating the DF Player mini on its own
- ✅ Operating the DF Player mini with speaker

### Monday 24/02

- 🔄 Watch a youtube video to understand wemos  
- 🔄 Watch a video to learn how to connect a website to a database
- ✅ Find the astra militarum emblem I'm going to use for my 3D model
- ✅ Find Seal of purity from astra militarum which I will use
- ✅ Find the model I'm going to start from to make my real model that I'll modify to make something I really like

---

## Third Week (Holidays):

### Thursday 20/02

- ✅ Start the assembly section
- ✅ Led and PIR sensor test program

### Tuesday 18/02

- ✅ I've added my Requirements section
- ✅ Transferred my audio files to my SD card

### Monday 17/02

- ✅ List of components: Arduino UNO, DFPlayer Module, ESP8266, PIR sensor, 2 red LEDs  
- ✅ Learning Fritzing  
- ✅ Connecting basic components and testing circuits  

---

## Second Week:

### Friday 14/02

- ✅ Resolution of table configuration errors  
- ✅ Troubleshooting Wemos connection problems  

### Thursday 13/02

- ✅ MySQL Workbench connection with teacher's help  
- ✅ Create database schema  
- ✅ Table configuration and index corrections  

### Wednesday 12/02

- ✅ Revision of database courses (ERD, relations)  
- ✅ Finalize database diagram  
- ✅ Addition of documentation and correction of audio files  

### Tuesday 11/02

- ✅ SG90 Servo Motor added to the circuit  
- ✅ Finalizing the circuit model  
- ✅ Cutting and preparing audio files  
- ✅ Start of website development (Front-end) 

### Monday 10/02

- ✅ List of components: Arduino UNO, DFPlayer Module, ESP8266, PIR sensor, 2 red LEDs  
- ✅ Learning Fritzing  
- ✅ Connecting basic components and testing circuits

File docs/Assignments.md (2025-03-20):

**System Architecture**

- 🔄 Introduction

- 🔄 LEGEND

- 🔄 DIAGRAM

**System Requirements**

- 🔄 DSENDING DATA TO BACKEND

- 🔄 RECEIVING DATA FROM BACKEND

- 🔄 AT LEAST TWO TYPES OF INPUT SENSORS

- 🔄 AT LEAST TWO TYPES OF VISUAL OR SENSORY OUTPUTS

- 🔄 WIFI MANAGER

**Technical Documentation**

- 🔄 DEDICATED APPLICATION FOR CREATING WIRING DIAGRAMS

- 🔄 VCC AND GND

- 🔄 HORIZONTAL AND VERITCAL WIRES/NETS

- 🔄 CORRECT PARTS

- 🔄 COLORS USED

- 🔄 POWER RAILS Vcc and GND

- 🔄 TABLE The Bill

- 🔄 COLUMN HEADINGS

- 🔄 ROWS WITH ACTUAL PARTS USED

- 🔄 FIELDS WITH RELEVANT/CORRECT CONTENTS

**Embedded Code**

- 🔄 AUTHOR AND LICENSE INFO AND GOAL OF THE PROGRAM

- 🔄 INDENTATION AND SYNTAX HIGHLIGHTING

- 🔄 MAGIC NUMBERS

- 🔄 COMMENTS

- 🔄 NO CODE DUPLICATION

- 🔄 NAMING CONVENTIONS

**Database**

- 🔄 All the sensor-data of the embedded device is stored in the database

- 🔄 The database is normalized into a correct relational database. Tool: MySQL Workbench

- 🔄 All the tables in the database have a logical and correct Primary Key

- 🔄 The structure of all the columns and tables is in such way that there is no data saved in a wrong format

- 🔄 The build script of your MySQL Database should be stored as .sql detailed instructions

**Technical Documentation + API Reference**

- 🔄 The REST API

- 🔄 There is a full explanation of the used technology

- 🔄 All the design choices are explained in detail of the front-end and back-end of the web application

**Application Code**

- 🔄 The front-end of the website is written in HTML, CSS and Javascript

- 🔄 The front-end gets it's data from the back-end by using Javascript HTTP calls

- 🔄 All externals (JS, CSS, images) are stored in its own files and included in the HTML

- 🔄 The code of the back-end is written in PHP, following the PSR-12 coding style

- 🔄 There is usage of include, functions and classes to prevent repetition of code

- 🔄 There is an API which is used by the front-end and embedded device. The API is the only entrance to the database

- 🔄 The back-end returns JSON-formatted text, always. So even if you add new data, you get a response in JSON

- 🔄 Every file contains a description, author and date

- 🔄 There are comments in the code where something can be unclear to the reader

**Concept & Design**

- 🔄 The user and the user needs are described

- 🔄 The main goal of the product is described

- 🔄 The product requirements (SMART) are provided

- 🔄 The desired physical product and the interaction with the product is demonstrated with visualisations

- 🔄 The choice for the digital manufacturing technique(s) and material(s) is justified

- 🔄 Choices for software are given

- 🔄 Design process is documented

- 🔄 Design files are proved

**Create & Test**

- 🔄 The chosen device(s) and material are described

- 🔄 Manufacturing settings that are used are given

- 🔄 Optimisations are described with their impact

- 🔄 The manufacturing process is logged with pictures and/or video’s as proof

- 🔄 Manufacturing files are present

- 🔄 Describe what (user) requirements you want to test

- 🔄 Describe how you are going tot test

- 🔄 Describe what works on your design and what you are going to change for you final version

- 🔄 Optimise your design according to your manual manufacturing experience

**Conclude & Reflect**

- 🔄 The product is Usable

- 🔄 It is described what requirements are (or are not) reached 

- 🔄 At least four failure during the design and creation process are given

**Research to market**

- ✅ Introduction / context

- ✅ Research question

- ✅ Research method

- 🔄 Implementation & Results

- 🔄 Conclusion

- 🔄 Recommendations

- 🔄 Sources and References

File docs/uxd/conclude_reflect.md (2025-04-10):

# Conclude & Reflect

Write here your own content!

## Reflection

The prototype of my connected calendar successfully meets most of the initial user and technical requirements:

- The interface allows appointments to be added, edited, and deleted.  
- The server functions perfectly and ensures smooth communication with the hardware.  
- Voice feedback works correctly both from the interface and through the physical sensors.  
- The cuckoo mechanism activates automatically every hour, as intended.

However, some features remain partially implemented or require further adjustment:

- The cuckoo is triggered with a one-minute delay, for an unknown reason.  
- I did not implement an audio notification when an appointment is reached, although it was part of the original concept.

---

## Issues Encountered

Throughout the process, I faced several challenges that helped me better understand the practical constraints of modeling and digital fabrication. Here are the main problems encountered:

---

## Incorrect sensor hole sizing (Tower)

- **Goal:** Print a tower with openings suited for the sensors  
- **Issue:** I miscalculated the dimensions and had to fully rebuild the tower.  
- **Temporary fix:** I corrected the STL file with accurate measurements.  
- **Next time:** I will first create a test plate to check dimensions before final printing.

---

## Poorly printed holes for the photoresistor

- **Goal:** Print functional holes to integrate the photoresistor.  
- **Issue:** The holes were not properly formed during printing.  
- **Solution:** I used a manual drill in another building to correct them.  
- **Future improvement:** Better orientation during printing and/or slightly larger holes.

Menu

Menu

Menu

Menu

---

## Button holes placed too close together

- **Goal:** Provide enough space for the wires and physical button.  
- **Issue:** The holes were too close to the edge, and the part had already been glued.  
- **Solution:** I cut the holes manually with a knife because it was too late to drill.  
- **Lesson learned:** Always validate critical spacing before final assembly. I now plan for extra margin around components.

Menu

Menu

Menu

---

## Incorrect LCD measurement

- **Goal:** Create a perfectly sized opening for the screen.  
- **Issue:** I measured it upside down, and the screen didn’t fit properly.  
- **Solution:** I had to force it into place.  
- **Next time:** I won’t take my measurements at 3 a.m.

Menu

---

## Not enough space for the photoresistor after wiring

- **Goal:** Neatly integrate all wires and components into the tower.  
- **Issue:** Once everything was installed, the photoresistor no longer fit and was sticking out.  
- **Solution:** I hid the part with a decorative flag.  
- **Planned improvement:** Plan cable routing more carefully and allow more free space during design.

Menu

Menu

---

To improve this project in a future version, I plan to:

- Add a voice notification when an appointment is reached  
- Fix the timing delay of the cuckoo  
- Redesign the internal layout of the tower to simplify wiring

## Product 

**The product from every angle**: [See the product](./turn.mp4)  

**The cuckoo comes out every hour followed by a sound**: [See the product](./sev.mp4)  

**The button does change the character voice, and there is a sound when you add, modify or delete an appointment. There's a motion detector, night mode and the fact that it reverts to daylight.**: [See the product](./all.mp4)

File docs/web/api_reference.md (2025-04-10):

# API reference

Write here your own content!

This API is used to manage appointments stored in the database. It is used by my site to add, retrieve, modify or delete data without reloading the page. The API is developed in PHP, and all responses are returned in JSON format. Requests are sent using fetch() on the JavaScript side.

---

## Database Connection

**Endpoint :** http://localhost/Database/Connection/database_connection.php  

**Description :** Establishes a connection to the MariaDB database using mysqli

This file is included in all PHP files that interact with the database.  
If the connection fails, the script stops and returns an error message.

## Parameters

| Variable | Value | Description |
|---|---|---|
| $host | mariadb | Hostname of the database |
| $user | root | Database username |
| $password  | 7YKyE8R2AhKzswfN | Database password |
| $database  | iot | Name of the database |

[database_connection.php  on GitLab](https://gitlab.fdmci.hva.nl/IoT/2024-2025-semester-2/individual-project/buudiizaaduu29/-/blob/main/web/Database/Connection/database_connection.php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)

---

## Insert a New Appointment

**Endpoint :** http://localhost/Database/Appointment/insert_appointment.php  
**Method :** POST  
**Description :** Create a new appointment for a device

## Request Parameters body: application/x-www-form-urlencoded

| Parameter | Type | Required | Description |
|---|---|---|---|
| task | string | Yes | Task |
| date_hour | string | Yes | Date and hour format: YYYY-MM-DD HH:MM:SS |
| device_id | int | Yes | Device ID |

## Success Response

```json
{
  "status": "success",
  "message": "Appointment added",
  "appointment_id": 5
}
```
### Error Responses

```json
{
  "status": "error",
  "message": "Task field is required"
}
```
```json
{
  "status": "error",
  "message": "Date and time field is required"
}
```
```json
{
  "status": "error",
  "message": "Device ID field is required and must be a number"
}
```
```json
{
  "status": "error",
  "message": "Wemos not connected"
}
```

[insert_appointment.php on GitLab](https://gitlab.fdmci.hva.nl/IoT/2024-2025-semester-2/individual-project/buudiizaaduu29/-/blob/main/web/Database/Appointment/insert_appointment.php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)

## Get Last Appointment

**Endpoint :** http://localhost/Database/Appointment/get_last_appointment.php  
**Method :** GET  
**Description :** Retrieve the last appointment saved in the system

## Request Parameters

No parameters required

## Success Response

```json
{
  "appointment_id": 3,
  "task": "Ready to die for the Emperor",
  "date_hour": "2025-03-20 17:05:00",
  "device_id": 1
}
```

## Error Response

```json
{
  "status": "error",
  "message": "No appointment found"
}
```
[get_last_appointment.php on GitLab](https://gitlab.fdmci.hva.nl/IoT/2024-2025-semester-2/individual-project/buudiizaaduu29/-/blob/main/web/Database/Appointment/get_last_appointment.php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)

## Update Appointment

**Endpoint :** http://localhost/Database/Appointment/update_appointment.php  
**Method :** PUT  
**Description :** Update an existing appointment by ID

## Request Body Content-Type: application/json

| Parameter | Type | Required | Description |
|---|---|---|---|
| appointment_id | int | Yes | ID of the appointment to update |
| task | string | Yes | Updated task description |
| date_hour | string | Yes | Updated date and time format: YYYY-MM-DD HH:MM:SS |

## Success Response

```json
{
  "status": "success",
  "message": "Appointment updated"
}
```

## Error Responses

```json
{
  "status": "error",
  "message": "Invalid request method, use PUT"
}
```

```json
{
  "status": "error",
  "message": "All fields are required."
}
```

```json
{
  "status": "error",
  "message": "SQL error: <detailed error message>"
}
```

[update_appointment.php  on GitLab](https://gitlab.fdmci.hva.nl/IoT/2024-2025-semester-2/individual-project/buudiizaaduu29/-/blob/main/web/Database/Appointment/get_last_appointment.php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)

## Get Last Updated Appointment

**Endpoint :** http://localhost/Database/Appointment/get_last_updated_appointment.php  
**Method :** GET  
**Description :** Retrieve the last updated appointment saved in a JSON file.

## Request Parameters

No parameters required

## Success Response

```json
{
  "appointment_id": 1,
  "task": "Fear ensures loyalty ! Where do you need me ?kkkkkkkkkkkkkkkkkkkkkkkkkkkkkkkkkkkkkkkkkkkkkkkkkkkkkkkk",
  "date_hour": "2025-03-14 15:00:00",
  "device_id": 1
}
```

## Error Response

```json
{
  "status": "error",
  "message": "No updated appointment found"
}
```

[get_last_updated_appointment.php on GitLab](https://gitlab.fdmci.hva.nl/IoT/2024-2025-semester-2/individual-project/buudiizaaduu29/-/blob/main/web/Database/Appointment/get_last_updated_appointment.php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)

## Delete Appointment

**Endpoint :** http://localhost/Database/Appointment/delete_appointment.php  
**Method :** DELETE  
**Description :** Delete an appointment by ID and return its data

## Request Body Content-Type: application/json

| Parameter | Type | Required | Description |
|---|---|---|---|
| appointment_id | int | Yes | ID of the appointment to delete |

## Success Response

```json
{
  "status": "success",
  "message": "Appointment deleted",
  "deleted_appointment": {
    "appointment_id": 1,
    "task": "Fear ensures loyalty ! Where do you need me ?kkkkkkkkkkkkkkkkkkkkkkkkkkkkkkkkkkkkkkkkkkkkkkkkkkkkkkkk",
    "date_hour": "2025-03-14 15:00:00",
    "device_id": 1,
    "note": "deleted"
  }
}
```

## Error Responses

```json
{
  "status": "error",
  "message": "Invalid request method, use DELETE"
}
```

```json
{
  "status": "error",
  "message": "Valid appointment ID is required."
}
```

```json
{
  "status": "error",
  "message": "Appointment not found"
}
```

```json
{
  "status": "error",
  "message": "Error: <SQL error message>"
}
```
[delete_appointment.php  on GitLab](https://gitlab.fdmci.hva.nl/IoT/2024-2025-semester-2/individual-project/buudiizaaduu29/-/blob/main/web/Database/Appointment/delete_appointment.php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)

## Get Last Deleted Appointment

**Endpoint :** http://localhost/Database/Appointment/get_last_deleted_appointment.php  
**Method :** GET  
**Description :** Retrieve the last deleted appointment saved in a JSON file.

## Request Parameters

No parameters required

## Success Response

```json
{
  "status": "success",
  "message": "Appointment deleted",
  "deleted_appointment": {
    "appointment_id": 1,
    "task": "Fear ensures loyalty ! Where do you need me ?kkkkkkkkkkkkkkkkkkkkkkkkkkkkkkkkkkkkkkkkkkkkkkkkkkkkkkkk",
    "date_hour": "2025-03-14 15:00:00",
    "device_id": 1,
    "note": "deleted"
  }
}
```

## Error Response

```json
{
  "status": "error",
  "message": "No deleted appointment found"
}
```

[get_last_deleted_appointment.php on GitLab](https://gitlab.fdmci.hva.nl/IoT/2024-2025-semester-2/individual-project/buudiizaaduu29/-/blob/main/web/Database/Appointment/get_last_deleted_appointment.php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)

## Get All Appointments

**Endpoint**: http://localhost/Database/Appointment/recover_appointment.php  
**Method**: GET  
**Description**: Retrieve all appointments from the database.

## Request Parameters

No parameters required

## Success Response

```json
[
  {
    "appointment_id": 5,
    "task": "Die for him",
    "date_hour": "2025-04-10 10:00:00",
    "note": "active",
    "device_id": 1
  },
  {
    "appointment_id": 7,
    "task": "By the Emperor it will be done !",
    "date_hour": "2025-04-11 15:30:00",
    "note": "active",
    "device_id": 1
  }
]
```

[recover_appointment.php  on GitLab](https://gitlab.fdmci.hva.nl/IoT/2024-2025-semester-2/individual-project/buudiizaaduu29/-/blob/main/web/Database/Appointment/recover_appointment.php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)

---

## Insert Device

**Endpoint :** http://localhost/Database/Device/insert_device.php  
**Method :** POST  
**Description :** Adds a new device or updates its IP address if it already exists.

## Request Parameters body: application/x-www-form-urlencoded

| Parameter | Type | Required | Description |
|---|---|---|---|
| name | string | Yes | Name of the device |
| ip_address  | string | Yes | IP address of the device  |

## Success Responses

```json
{
  "status": "success",
  "message": "New device added successfully.",
  "device": {
    "device_id": 1,
    "name": "ESP32",
    "ip_address": "100.74.254.22"
  }
}
```

## Error Responses

```json
{
  "status": "error",
  "message": "Please fill in all required fields."
}

```
```json
{
  "status": "error",
  "message": "SQL error message"
}

```

[insert_device.php on GitLab](https://gitlab.fdmci.hva.nl/IoT/2024-2025-semester-2/individual-project/buudiizaaduu29/-/blob/main/web/Database/Device/insert_device.php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)

## Delete Device

**Endpoint :** http://localhost/Database/Device/delete_device.php  
**Method :** POST  
**Description :** Delete a device from the database using its ID.

## Request Parameters body: application/x-www-form-urlencoded

| Parameter | Type | Required | Description |
|---|---|---|---|
| device_id | int | Yes | ID of the device to be deleted |

## Success Response

```json
{
  "status": "success",
  "message": "Device with ID 3 successfully deleted."
}
```

## Error Responses

```json
{
  "status": "error",
  "message": "Missing or invalid device ID."
}
```

```json
{
  "status": "error",
  "message": "Device with ID 3 does not exist."
}
```

```json
{
  "status": "error",
  "message": "Error while deleting the device."
}
```

```json
{
  "status": "error",
  "message": "Invalid request method."
}
```

[delete_device.php on GitLab](https://gitlab.fdmci.hva.nl/IoT/2024-2025-semester-2/individual-project/buudiizaaduu29/-/blob/main/web/Database/Device/delete_device.php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)

## Get All Devices

**Endpoint :** http://localhost/Database/Device/recover_device.php  
**Method :** GET  
**Description :** Retrieve all devices from the database and save them in a JSON file.

## Request Parameters

No parameters required

## Success Response

```json
{
  "status": "success",
  "devices": [
    {
      "device_id": 1,
      "name": "ESP32",
      "ip_address": "100.74.254.22"
    }
  ]
}
```

## Error Response

```json
{
  "status": "error",
  "message": "No devices found."
}
```

[recover_device.php on GitLab](https://gitlab.fdmci.hva.nl/IoT/2024-2025-semester-2/individual-project/buudiizaaduu29/-/blob/main/web/Database/Device/recover_device.php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)

---

## Insert Sensor

**Endpoint :** http://localhost/Database/Sensor/insert_sensor.php  
**Method :** POST  
**Description :** Add a new sensor for a specific device.

## Request Parameters body: application/x-www-form-urlencoded

| Parameter | Type | Required | Description |
|---|---|---|---|
| name | string | Yes | Name of the sensor |
| type | string | Yes | Type of the sensor (e.g., temperature) |
| activation_threshold | float  | No | Value at which the sensor activates |
| device_id | int | Yes | ID of the device the sensor is linked to |

## Success Response

```json
{
  "status": "success",
  "message": "Sensor added successfully.",
  "sensor": {
    "sensor_id": 3,
    "name": "Photoresistor",
    "type": "Light",
    "activation_threshold": 700,
    "device_id": 1
  }
}
```

## Error Responses

```json
{
  "status": "error",
  "message": "A sensor with this name already exists for this device."
}
```

```json
{
  "status": "error",
  "message": "Please fill in all required fields."
}
```

```json
{
  "status": "error",
  "message": "SQL error message"
}
```

[insert_sensor.php on GitLab](https://gitlab.fdmci.hva.nl/IoT/2024-2025-semester-2/individual-project/buudiizaaduu29/-/blob/main/web/Database/Sensor/insert_sensor.php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)

## Delete Sensor

**Endpoint :** http://localhost/Database/Sensor/delete_sensor.php  
**Method :** POST  
**Description :** Delete a sensor from the database using its ID.

## Request Parameters body: application/x-www-form-urlencoded

| Parameter | Type | Required | Description |
|---|---|---|---|
| sensor_id | int | Yes | ID of the sensor to be deleted |

## Success Response

```json
{
  "status": "success",
  "message": "Sensor with ID 4 successfully deleted."
}
```

## Error Responses

```json
{
  "status": "error",
  "message": "Missing or invalid sensor ID."
}
```

```json
{
  "status": "error",
  "message": "Sensor with ID 4 does not exist."
}
```

```json
{
  "status": "error",
  "message": "Error while deleting the sensor."
}
```

```json
{
  "status": "error",
  "message": "Invalid request method."
}
```

[delete_sensor.php on GitLab](https://gitlab.fdmci.hva.nl/IoT/2024-2025-semester-2/individual-project/buudiizaaduu29/-/blob/main/web/Database/Sensor/delete_sensor.php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)

## Get All Sensors

**Endpoint :** http://localhost/Database/Sensor/recover_sensor.php  
**Method :** GET  
**Description :** Retrieve all sensors from the database.

## Request Parameters

No parameters required

## Success Response

```json
{
  "status": "success",
  "sensors": [
    {
      "sensor_id": 1,
      "name": "Button",
      "type": "Button",
      "activation_threshold": 1,
      "device_id": 1
    },
    {
      "sensor_id": 2,
      "name": "PIR",
      "type": "Presence",
      "activation_threshold": 0,
      "device_id": 1
    },
    {
      "sensor_id": 3,
      "name": "Photoresistor",
      "type": "Light",
      "activation_threshold": 700,
      "device_id": 1
    }
  ]
}
```

## Error Responses

```json
{
  "status": "error",
  "message": "No sensors found."
}
```

```json
{
  "status": "error",
  "message": "Invalid request."
}
```

[recover_sensor.php on GitLab](https://gitlab.fdmci.hva.nl/IoT/2024-2025-semester-2/individual-project/buudiizaaduu29/-/blob/main/web/Database/Sensor/recover_sensor.php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)

---

## Insert Sensor Data 3 Sensors

**Endpoint :** http://localhost/Database/SensorData/insert_sensor_data.php  
**Method :** POST  
**Description :** Insert sensor data for 3 sensors and keep only the latest 20 records per sensor.

## Request Parameters body: application/x-www-form-urlencoded

| Parameter | Type | Required | Description |
|---|---|---|---|
| sensor_id_1 | int | Yes | First sensor ID |
| value_1 | float | Yes | Value for first sensor |
| sensor_id_2 | int  | Yes | Second sensor ID |
| value_2 | float | Yes | Value for second sensor |
| sensor_id_3 | int | Yes | Third sensor ID |
| value_3 |float | Yes | Value for third sensor |

## Success Response

```json
{
  "status": "success",
  "message": "Sensor data inserted successfully and old entries cleaned.",
  "data": [
    {
      "sensor_id": 1,
      "value": 22.3,
      "timestamp": "2025-04-09 14:30:00"
    },
    {
      "sensor_id": 2,
      "value": 59.2,
      "timestamp": "2025-04-09 14:30:00"
    },
    {
      "sensor_id": 3,
      "value": 18.6,
      "timestamp": "2025-04-09 14:30:00"
    }
  ]
}
```

## Error Responses

```json
{
  "status": "error",
  "message": "Missing data."
}
```
```json
{
  "status": "error",
  "message": "Invalid request."
}
```

[insert_sensor_data.php on GitLab](https://gitlab.fdmci.hva.nl/IoT/2024-2025-semester-2/individual-project/buudiizaaduu29/-/blob/main/web/Database/SensorData/insert_sensor_data.php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)

## Get Latest Sensor Data

**Endpoint :** http://localhost/Database/SensorData/recover_sensor_data.php  
**Method :** GET  
**Description :** Retrieve the latest 20 sensor data entries, grouped by sensor

## Request Parameters

No parameters required

## Success Response

```json
{
  "status": "success",
  "sensors": {
    "1": [
      {
        "value": 0,
        "timestamp": "2025-04-01 13:39:10"
      },
      {
        "value": 0,
        "timestamp": "2025-04-01 13:32:22"
      },
      {
        "value": 1,
        "timestamp": "2025-04-01 13:25:18"
      },
      {
        "value": 1,
        "timestamp": "2025-04-01 13:25:12"
      },
      {
        "value": 1,
        "timestamp": "2025-04-01 13:24:59"
      },
      {
        "value": 1,
        "timestamp": "2025-04-01 13:24:53"
      }
    ],
    "2": [
      {
        "value": 1,
        "timestamp": "2025-04-01 13:39:10"
      },
      {
        "value": 1,
        "timestamp": "2025-04-01 13:32:22"
      },
      {
        "value": 0,
        "timestamp": "2025-04-01 13:25:18"
      },
      {
        "value": 0,
        "timestamp": "2025-04-01 13:25:12"
      },
      {
        "value": 0,
        "timestamp": "2025-04-01 13:24:59"
      },
      {
        "value": 0,
        "timestamp": "2025-04-01 13:24:53"
      },
      {
        "value": 0,
        "timestamp": "2025-04-01 13:24:51"
      }
    ],
    "3": [
      {
        "value": 0,
        "timestamp": "2025-04-01 13:39:10"
      },
      {
        "value": 0,
        "timestamp": "2025-04-01 13:32:22"
      },
      {
        "value": 0,
        "timestamp": "2025-04-01 13:25:18"
      },
      {
        "value": 0,
        "timestamp": "2025-04-01 13:25:12"
      },
      {
        "value": 0,
        "timestamp": "2025-04-01 13:24:59"
      },
      {
        "value": 0,
        "timestamp": "2025-04-01 13:24:53"
      },
      {
        "value": 0,
        "timestamp": "2025-04-01 13:24:51"
      }
    ]
  }
}
```

## Error Responses

```json
{
  "status": "error",
  "message": "Error while retrieving sensor data."
}
```

```json
{
  "status": "error",
  "message": "Invalid method."
}
```

[recover_sensor_data.php on GitLab](https://gitlab.fdmci.hva.nl/IoT/2024-2025-semester-2/individual-project/buudiizaaduu29/-/blob/main/web/Database/SensorData/recover_sensor_data.php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)

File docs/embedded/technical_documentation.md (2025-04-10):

# Technical documentation

Your Wiring Diagram, Bill of Materials, ... everything about how you built your embedded device should be documented here.

## Wiring Diagram

This Fritzing diagram shows the wiring of the ESP32-based Smart Calendar system. It includes the connection of several hardware components: an I2C LCD, a 7-segment display (TM1637), a DFPlayer Mini audio module, a servo motor, a PIR sensor, a brightness sensor (LDR), and a push-button. The aim is to visualize the project's physical architecture in order to facilitate assembly.

Menu

---

## ESP32 ( Inputs )

__Button :__

Connected to PIN D14

VCC : 3.3 V

Resistance of 10k Ohm

__Photoresistor :__

Connected to PIN D34

VCC : 3.3 V

Resistance of 10k Ohm

__PIR Sensor:__

Connected to PIN D35

VCC : 5 V

---

## ESP32 ( Outputs )

__4 digits display :__

Connected to PIN D18 **CLK**

Connected to PIN D19 **DIO**

VCC : 3.3 V

__SV90 Servo :__

Connected to PIN D27

VCC : 5 V

__LCD Screen :__ 

Connected to PIN D22 **SCL**

Connected to PIN D21 **SDA**

VCC : 5 V

__DF Player Mini :__

Connected to PIN RX2 **TX**

Connected to PIN TX2 **RX**

VCC : 5 V

Resistance of 10k Ohm for **RX**

__Speaker :__

Connected to PIN SPK_1 **on DF Player mini**

Connected to PIN SPK_2 **on DF Player mini**

## ESP32 USB-C

Connected to the computer

Used as a power supply

Used to upload code

5V 

1A

---

## **Bill of Materials**

This table lists all the components required to build the ESP32-based Smart Calendar System. Each item includes a description, the quantity used in the project, the estimated price (including VAT), and a link to an example supplier. These components provide the system's main functions: display, sensor reading, network communication and user interaction.

| Part # | Manufacturer | Description | Qty | Price | Subtotal | Example URL | Extra Info |
|---|---|---|---|---|---|---|---|
| ESP32-DEV | Espressif | ESP32 dev board WiFi/Bluetooth | 1 | 9.00 € | 9.00 € | [Link](https://www.tinytronics.nl/en/development-boards/microcontroller-boards/with-wi-fi/esp32-wifi-and-bluetooth-board-cp2102) | [Datasheet](https://www.espressif.com/sites/default/files/documentation/esp32_datasheet_en.pdf) |
| TACT-6x6x5 | Not specified  | Tactile push button (momentary) | 1 | 0.10 € | 0.10 € | [Link](https://www.tinytronics.nl/en/switches/manual-switches/pcb-switches/tactile-push-button-switch-momentary-4pin-6*6*5mm) | [More infos](https://components101.com/switches/push-button) |
| GL5528-LDR | Not specified  | Light dependent resistor (LDR) | 1 | 0.30 € | 0.30 € | [Link](https://www.tinytronics.nl/en/sensors/optical/light-and-color/gl5528-ldr-light-sensitive-resistor) | [Datasheet](https://components101.com/sites/default/files/component_datasheet/LDR%20Datasheet.pdf) |
| PIR-HC-SR501 | Not specified  | PIR motion sensor module | 1 | 3.50 € | 3.50 € | [Link](https://www.tinytronics.nl/en/sensors/motion/ir-pyroelectric-infrared-pir-motion-sensing-detector-module) | [Datasheet](https://cdn-learn.adafruit.com/downloads/pdf/pir-passive-infrared-proximity-motion-sensor.pdf) |
| 4SEG-COM-RED | Not specified  | 4-digit 7-segment display (red) | 1 | 1.25 € | 1.25 € | [Link](https://www.tinytronics.nl/en/displays/segments/segmenten-display-4-characters-red) | [Datasheet](https://www.farnell.com/datasheets/2095876.pdf) |
| SG90 | TianKongRC | SG90 Mini Servo | 1 | 3.25 € | 3.25 € | [Link](https://www.tinytronics.nl/en/mechanics-and-actuators/motors/servomotors/sg90-mini-servo) | [Datasheet](https://www.friendlywire.com/projects/ne555-servo-safe/SG90-datasheet.pdf) |
| LCD-16x2-BL | Not specified  | LCD 16x2 blue backlight display | 1 | 3.50 € | 3.50 € | [Link](https://www.tinytronics.nl/en/displays/lcd/lcd-display-16*2-characters-with-white-text-and-blue-backlight) | [Datasheet](https://www.vishay.com/docs/37484/lcd016n002bcfhet.pdf) |
| DFPlayerMini | DFRobot | Mini MP3 Player Module | 1 | 8.00 € | 8.00 € | [Link](https://www.tinytronics.nl/en/audio/audio-sources/dfrobot-dfplayer-mini-mp3-module) | [Datasheet](https://picaxe.com/docs/spe033.pdf) |
| WS-14595 | Waveshare | Speaker set - 8Ω 5W | 1 | 6.75 € | 6.75 € | [Link](https://www.tinytronics.nl/en/audio/speakers/speakers/waveshare-speaker-set-8%CF%89-5w) | Rated power: 5W, Impedance: 8Ω, Four 6.5mm mounting holes, Dimensions: 99 x 44.5 x 21mm |
| BB-170-WHITE | Not specified  | Breadboard 170 points (white) | 2 | 1.00 € | 2.00 € | [Link](https://www.tinytronics.nl/en/tools-and-mounting/prototyping-supplies/breadboards/breadboard-170-points-white) | [Datasheet](https://www.farnell.com/datasheets/4024568.pdf) |
| BB-PWR-3.3V-5V | Not specified  | Breadboard power supply | 1 | 2.50 € | 2.50 € | [Link](https://www.tinytronics.nl/en/power/voltage-converters/voltage-regulators/breadboard-power-supply-5v-en-3.3v) | [Datasheet](https://www.handsontec.com/dataspecs/mb102-ps.pdf) |
| DUP-MF-10CM | Not specified  | Jumper wire M-F 10cm (x10) | 2 packs | 0.50 € | 1.00 € | [Link](https://www.tinytronics.nl/en/cables-and-connectors/cables-and-adapters/prototyping-wires/dupont-compatible-and-jumper/dupont-jumper-wire-male-female-10cm-10-wires) | 11 used, 20 total |
| DUP-MM-10CM | Not specified  | Jumper wire M-M 10cm (x10) | 2 packs | 0.50 € | 1.00 € | [Link](https://www.tinytronics.nl/en/cables-and-connectors/cables-and-adapters/prototyping-wires/dupont-compatible-and-jumper/dupont-jumper-wire-male-male-10cm-10-wires) | 11 used, 20 total |
| RES-10K-5% | Not specified  | 10kΩ Resistor (±5%) | 2 | 0.05 € | 0.10 € | [Link](https://www.tinytronics.nl/en/components/resistors/resistors/10k%CF%89-resistor-(standard-pull-up-or-pull-down-resistor)) | [Datasheet](https://www.seielect.com/Catalog/SEI-CF_CFM.pdf) |
| USB-C | Cuxnoo | USB-C | 1 | 12.00 € | 12.00 € | [Link](https://www.amazon.nl/C-videokabel-Cuxnoo-C-monitorkabel-ondersteunt-gegevenssynchronisatie/dp/B089ST58C5/) | USB-C to USB-C, supports fast charging and data sync |

### Total = 66.74 €

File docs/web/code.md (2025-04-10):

# Web Code

Write here your own content!

## Project Structure

The project is structured in a clean and modular way :

```
📁 root/
├── index.html                        # Main homepage with loading screen + terminal
├── inside_spirit_machine.html        # Calendar + sensor-based interface
├── style.css                         # Custom design + Tailwind overrides
├── script.js                         # Front-end logic & API calls
├── /images/tech_priest.png           # Static assets
├── /models/Astra_Militarum.stl       # 3D STL model for viewer
└── Database/
    └── Appointment/
        ├── insert_appointment.php    # POST: Add a new appointment
        ├── recover_appointment.php   # GET: Retrieve all appointments
        ├── update_appointment.php    # PUT: Edit an appointment
        └── delete_appointment.php    # DELETE: Remove an appointment
```

---

I followed code practices for every language used :

## JavaScript

- All functions are written in camelCase
- API calls use fetch() with clear HTTP methods
- DOM interactions are grouped logically
- Code is fully commented and structured

## PHP

- Each route is in its own file 
- Responses are returned in consistent JSON format
- Prepared statements are used to prevent SQL injection

## HTML / CSS

- HTML structure 
- CSS is modular, separated from HTML
- Used Tailwind CSS + custom utility classes
- Animations and transitions are abstracted with clean class names

All source files include a comment header with:

- Description  
- Author   
- Date

And the key functions are explained with inline comments

---

## JavaScript Adding an Appointment

This function collects user input and sends a POST request to the backend API.

```js
function ism_addAppointment() {
  const task = document.getElementById("ism-appointmentTitle").value;
  const date_hour = document.getElementById("ism-appointmentDateTime").value;
  const device_id = 1;

  fetch("Database/Appointment/insert_appointment.php", {
    method: "POST",
    headers: { "Content-Type": "application/x-www-form-urlencoded" },
    body: `task=${task}&date_hour=${date_hour}&device_id=${device_id}`
  })
  .then(response => response.json())
  .then(data => {
    if (data.status === "success") {
      ism_loadAppointments();
    }
  });
}
```

---

## PHP

This endpoint receives appointment data and inserts it into the database.

```php
<?php
// Include the database connection file
require __DIR__ . '/../Connection/database_connection.php';

// Check if the request method is POST
if ($_SERVER["REQUEST_METHOD"] == "POST") 
{
    // Check if task is set and not empty
    if (isset($_POST['task']) && trim($_POST['task']) !== '') 
    {
        $task = trim($_POST['task']);
    } 
    
    else 
    {
        // Return error if task is missing
        echo json_encode(["status" => "error", "message" => "Task field is required"]);
        exit;
    }

    // Check if date_hour is set and not empty
    if (isset($_POST['date_hour']) && trim($_POST['date_hour']) !== '') 
    {
        $date_hour = trim($_POST['date_hour']);
    } 

    else 
    {
        // Return error if date_hour is missing
        echo json_encode(["status" => "error", "message" => "Date and time field is required"]);
        exit;
    }

    // Check if device_id is set and is a number
    if (isset($_POST['device_id']) && is_numeric($_POST['device_id'])) 
    {
        $device_id = intval($_POST['device_id']);
    } 

    else 
    {
        // Return error if device_id is missing or invalid
        echo json_encode(["status" => "error", "message" => "Device ID field is required and must be a number"]);
        exit;
    }

    // Double check if any field is still empty
    if (empty($task) || empty($date_hour) || empty($device_id)) 
    {
        echo json_encode(["status" => "error", "message" => "All fields are required"]);
        exit;
    }

    // Check if the device exists in the database
    $check_device = $link->prepare("SELECT device_id FROM Device WHERE device_id = ?");
    $check_device->bind_param("i", $device_id);
    $check_device->execute();
    $result = $check_device->get_result();

    if ($result->num_rows === 0) 
    {
        // Return error if device is not found
        echo json_encode(["status" => "error", "message" => "Wemos not connected"]);
        exit;
    }

    // Set default note value
    $note = "active";

    // Insert the new appointment into the database
    $stmt = $link->prepare("INSERT INTO Appointment (task, date_hour, note, device_id) VALUES (?, ?, ?, ?)");
    $stmt->bind_param("sssi", $task, $date_hour, $note, $device_id);

    if ($stmt->execute()) 
    {
        // Return success with the new appointment ID
        echo json_encode(["status" => "success", "message" => "Appointment added", "appointment_id" => $stmt->insert_id]);
    } 

    else 
    {
        // Return error if insertion failed
        echo json_encode(["status" => "error", "message" => "Error: " . $stmt->error]);
    }

    // Close statements and connection
    $stmt->close();
    $check_device->close();
    $link->close();
} 

else 
{
    // Return error if request method is not POST
    echo json_encode(["status" => "error", "message" => "Invalid request"]);
}
?>
```

---

## CSS

This example shows how I style a full-width background and a custom button

```css
.background-section {
  width: 100%;
  height: 100vh;
  background-image: url('Home_page.png');
  background-size: cover;
  background-position: center;
  display: flex;
  justify-content: center;
  align-items: flex-start;
}

.button {
  background-color: #8b0000;
  color: white;
  padding: 10px 20px;
  border-radius: 5px;
  text-transform: uppercase;
}
```

[GitLab](https://gitlab.fdmci.hva.nl/IoT/2024-2025-semester-2/individual-project/buudiizaaduu29/-/tree/main/web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)

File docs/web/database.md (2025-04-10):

# Database

Write here your own content!

## ERD Diagram

menu

## Database Schema

menu

## Table Structures

## Device Table

```sql
CREATE TABLE IF NOT EXISTS `iot`.`Device` (
  `device_id` INT NOT NULL AUTO_INCREMENT,
  `name` VARCHAR(20) NOT NULL,
  `ip_address` VARCHAR(15) NOT NULL,
  PRIMARY KEY (`device_id`),
  UNIQUE INDEX `ip_address_UNIQUE` (`ip_address` ASC) VISIBLE)
ENGINE = InnoDB;
```

**Explanation:**

Primary Key: device_id (INT AUTO_INCREMENT), unique identifier for each device

**Attributes :**

- name: Name of the device
- ip_address: Unique IP address on the network

**Index :**

On ip_address to ensure uniqueness and speed up searches

## Appointment Table

```sql
CREATE TABLE IF NOT EXISTS `iot`.`Appointment` (
  `appointment_id` INT NOT NULL AUTO_INCREMENT,
  `task` VARCHAR(255) NOT NULL,
  `date_hour` DATETIME NOT NULL,
  `note` VARCHAR(7) NOT NULL,
  `device_id` INT NOT NULL,
  PRIMARY KEY (`appointment_id`),
  INDEX `date_hour` (`date_hour` ASC) VISIBLE,
  INDEX `fk_appointment` (`device_id` ASC) VISIBLE,
  CONSTRAINT `fk_appointment`
    FOREIGN KEY (`device_id`)
    REFERENCES `iot`.`Device` (`device_id`)
    ON DELETE CASCADE
    ON UPDATE CASCADE)
ENGINE = InnoDB;
```

**Explanation :**

Primary Key: appointment_id (INT AUTO_INCREMENT)
Foreign Key: device_id referencing Device table

**Attributes:**

- task: Task description
- date_hour: Combined date and time (DATETIME)
- note: Additional note (limited to 7 characters)

**Index :**

On date_hour to optimize date searches

**Relationship :**

1 device can have N appointments (1:N)

## Sensor Table

```sql
CREATE TABLE IF NOT EXISTS `iot`.`Sensor` (
  `sensor_id` INT NOT NULL AUTO_INCREMENT,
  `name` VARCHAR(45) NOT NULL,
  `type` ENUM('Presence', 'Light', 'Button') NOT NULL,
  `activation_threshold` FLOAT NULL,
  `device_id` INT NOT NULL,
  PRIMARY KEY (`sensor_id`),
  INDEX `type` (`type` ASC) VISIBLE,
  INDEX `fk_sensor` (`device_id` ASC) VISIBLE,
  CONSTRAINT `fk_sensor`
    FOREIGN KEY (`device_id`)
    REFERENCES `iot`.`Device` (`device_id`)
    ON DELETE CASCADE
    ON UPDATE CASCADE)
ENGINE = InnoDB;
```

**Explanation :**

Primary Key: sensor_id (INT AUTO_INCREMENT)
Foreign Key: device_id referencing Device table

**Attributes :**

- name: Sensor name
- type: Predefined type
- activation_threshold: Activation threshold

**Index :**

On type to facilitate sensor type searches

**Relationship :**

1 device can have N sensors (1:N)

### SensorData Table

```sql
CREATE TABLE IF NOT EXISTS `iot`.`SensorData` (
  `data_id` INT NOT NULL AUTO_INCREMENT,
  `value` FLOAT NOT NULL,
  `time_stamp` DATETIME NOT NULL,
  `button_state` TINYINT NULL DEFAULT 0,
  `sensor_id` INT NOT NULL,
  PRIMARY KEY (`data_id`),
  INDEX `timestamp` (`time_stamp` ASC) VISIBLE,
  INDEX `fk_data` (`sensor_id` ASC) VISIBLE,
  CONSTRAINT `fk_data`
    FOREIGN KEY (`sensor_id`)
    REFERENCES `iot`.`Sensor` (`sensor_id`)
    ON DELETE CASCADE
    ON UPDATE CASCADE)
ENGINE = InnoDB;
```

**Explanation :**

Primary Key: data_id (INT AUTO_INCREMENT)
Foreign Key: sensor_id referencing Sensor table

**Attributes :**

- value: Numeric sensor value
- time_stamp: Measurement timestamp
- button_state: Button state (0/1)

**Index :**

On time_stamp to optimize time-based queries

**Relationship :**

1 sensor can generate N data entries (1:N)

## Normalization and Conventions

The database complies with the third normal form:
- No data redundancy
- All dependencies are towards primary keys
- No transitive dependencies

**Conventions used :**

- Table names in PascalCase
- Column names in lowercase_with_underscores
- Primary keys named as table_id
- Foreign keys referenced with fk_ prefix

## Example Insertions

**Device insertion :**

```sql
INSERT INTO Device (name, ip_address)
VALUES ('Wemos', '192.168.1.10');
```

**Appointment insertion:**

```sql
INSERT INTO Appointment (task, date_hour, note, device_id)
VALUES ('Ready to die for him', '2023-12-15 14:30:00', 'urgent', 1);
```

**Sensor insertion:**

```sql
INSERT INTO Sensor (name, type, activation_threshold, device_id)
VALUES ('PIR', 'Presence', 0, 1);
```

**SensorData insertion :**

```sql
INSERT INTO SensorData (value, time_stamp, button_state, sensor_id)
VALUES (1.2, NOW(), NULL, 1);
```

## Detailed Guide for SQL Script Usage

### Step 1

**Install MySQL Server:**

- Download MySQL Community Server
- Follow the installation instructions according to your operating system

**Install MySQL Workbench:**

- Download MySQL Workbench
- Install and launch the application to confirm installation

## Step 2

- Open MySQL Workbench
- Click on MySQL Connections to configure a new connection:
  - Click on "+"
  - Enter the following:
    - Connection Name: iot
    - Hostname: mariadb
    - Port: 3306
    - Username: root
  - Click OK

## Step 3

Select your connection (iot) and click Open
In the SQL window, create the database by executing:

```sql
CREATE DATABASE iot;
USE iot;
```

Execute your full SQL script:
- Open your SQL script (forward_engineer.sql) in MySQL Workbench
- Click the "Execute" icon (lightning bolt) to run the entire script.

## Step 4

Create a specific user to access your database:

```sql
CREATE USER 'iot_user'@'localhost' IDENTIFIED BY 'user_password';
GRANT ALL PRIVILEGES ON iot.* TO 'iot_user'@'localhost';
FLUSH PRIVILEGES;
```

## Step 5

Refresh the list of databases and tables
Check that these 4 tables are created:
- Device
- Appointment
- Sensor
- SensorData

Your `iot` database is now perfectly configured and ready for use.

## Link to SQL Script

[SQL Script](https://gitlab.fdmci.hva.nl/IoT/2024-2025-semester-2/individual-project/buudiizaaduu29/-/blob/main/Victor/Database/forward_engineer.sql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)

## Future Improvements

- Add a description field to the Sensor table
- Implement triggers for data validation
- Add views for frequent queries
- Extend ENUM types for sensors for more flexibility

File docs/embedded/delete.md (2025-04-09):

## 8Ω Speaker

- Available on Amazon for **10,59 €**

Speaker

🔗 [View on Amazon](https://www.amazon.fr/Haut-Parleur-Fr%C3%A9quence-Ordinateur-Interface-JST-PH2-0/dp/B08QFTYB9Z/ref=sr_1_2)

---

## Mini MP3 DFPlayer Module

- Available on Amazon for **9,99 €**

MP3 Module

🔗 [View on Amazon](https://www.amazon.fr/KeeYees-Lecteur-Bricolage-Compatible-Lautsprecher/dp/B07X2CZZDJ/ref=sr_1_5)

---

## SD Card

- Available on Amazon for **11,99 €** (3,00 € / unit) ( Just need 1 SD Card so 3,00 € )

SD Card

🔗 [View on Amazon](https://www.amazon.fr/Cloudisk-2Pack-m%C3%A9moire-MicroSD-Classe/dp/B08L8T86TS/ref=sr_1_2_sspa)

---

## PIR Sensor

- Available on Amazon for **3,89 €**

PIR_sensor

🔗 [View on Amazon](https://www.amazon.fr/OcioDual-Mouvement-D%C3%A9tecteur-Pyro-%C3%A9lectrique-Infrarouge/dp/B071FBG4XW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)

---

## 0.96” OLED display 128x64 I2C/SPI

- Available on Amazon for **6,89 €**

screen

🔗 [View on Amazon](https://www.amazon.fr/dp/B0CX6HHW3D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)

---

## Red Led

- Available on Amazon for **5,75 €** (0,06 € / unit) ( Just need 2 LED so 0.12 € )

led

🔗 [View on Amazon](https://www.amazon.fr/100-LED-broches-Couleur-Lumi%C3%A8re-Arduino/dp/B00HD4P1XW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)

---

## Resistor kit

- Available on Amazon for **6,99 €** (0,0125€ € / unit) ( Just need 4 resistors so 0,05€ € )

resistor

🔗 [View on Amazon](https://www.amazon.fr/DollaTek-R%C3%A9sistances-Carbone-Assorties-Valeurs/dp/B07DJ5644W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)

---

## Servomotor

- Available on Amazon for **10,99 €** (2,75 € / unit) ( Just need 1 Servomotor so 2,75 € )

servomotor

🔗 [View on Amazon](https://www.amazon.fr/Servomoteur-Binghe-Servo-Micromoteurs-H%C3%A9licopt%C3%A8res/dp/B0DGT6SCLQ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)

---

## Wemos D1 Mini

- Available on Amazon for **9,99 €** (3,33 € / unit) ( Just need 1 Servomotor so 3,33 € )

wemos

🔗 [View on Amazon](https://www.amazon.fr/ESP8266-Binghe-d%C3%A9veloppement-Interface-Compatible/dp/B0D7C2WM9G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)

---

## Wire

- Available on Amazon for **7,69 €** 

wire

🔗 [View on Amazon](https://www.amazon.fr/AZDelivery-Jumper-Cavalier-C%C3%A2ble-Arduino/dp/B074P726ZR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)

---

## Wire

- Available on Amazon for **26,21 €** 

arduino

🔗 [View on RobotShop](https://eu.robotshop.com/nl/products/arduino-uno-rev3-smd)

---

## Total  

- **89,41 €** 

CC#01 Program code contains comment in the top the file stating:
// 1. author information
// 2. goal of this part of the program
// 3. license type.

---

CC#02 Program code (single lines of code, code constructs, code blocks, functions) is consequently indented with tabs or spaces for readability. 
Code blocks contain matching curly brackets { }.

---

CC#03 Program code does not contain magic numbers (for readability and maintainability)

---

CC#04 Program code is commented

---

CC#05 Program is written in a way that does not lead to code duplication.

---

CC#06 There are consequent naming conventions for variables and functions

My home page :

When you first enter my website, I made sure to add a loading screen that simulates a human heartbeat to match the theme of my smart calendar. At first, it wasn't planned at all: my girlfriend had sent me a video on TikTok with someone who presented different ways of making loading screens.

 Why the heartbeat simulation? It's all explained on my home page. After a few seconds of loading, you're greeted by a technopriest, with a machine representing the Machine God in the background. The Machine God, also known as the Omnissiah or Deus Mechanicus, is the supernatural entity worshipped by the tech-priests and other servants of the Adeptus Mechanicus as the embodiment and bestower of all knowledge and technology in the universe of Warhammer 40,000. 
 
 As for the text there, this text allows me to explain to users which blueprint I've chosen, explaining it as if it were the Techpriest speaking with unfailing devotion to the God of the machine, and to explain what awaits the user once he decides to enter his data.

My page where the user can interact :

On this page, I've put an image in the background showing a technopriest praying to the machine God with 2 other technopriests, with text above to remind the user once again what he can do.

Once you've decided to enter your data, there are 2 places where you can enter your data: the name of your task, and the time and minute information. If the user wants to change any information, he can do so. He can also delete any task he wants and modify any task already entered.

---

## 3 weeks ago

I'm going to take the liberty of talking about the very first code I've just made, even though I admit I'd have preferred it to be on the Arduino, but I realized that the components I wanted to use I don't have. I'll be receiving them on Saturday, so to save time I decided to take care of the front-end of my website. I'd already done some because I'd been lucky enough to work for a medical practice and had taken care of their website. So my very first code is an html file in the Warhammer 40,000 universe. I'm so happy with what I've accomplished! I'm really proud of myself for having succeeded in making something that suits me. It was important for me to be able to add my favorite universe to this project. In this HTML file I put an image in the background to give the image a theme, I decided to add a text area with an image of a tech priest that gives the impression of talking to us with a button at the bottom when we're ready to commune with the machine spirit.

Regarding what I did last night, I started by changing my text because the feedback I'd received told me it wasn't really clear, so I wanted to change that first. I continued by adding a text first to make them understand what they're supposed to do, I just hope the texts aren't too long. After making the text I put a button that would allow me to display or not the fact of being able to add an apointment, I added the possibility of adding a date, time and task that the user wanted. And finally I added an option to delete if the user has mistakenly added an appointment he didn't want.

## Appointment

Concerning the appointment part, I use several APIs, in particular 4, an API that lets me send an appointment from my website to the database, an API that lets me delete it from my website and modify it.
The last API I use allows me to retrieve the appointments I have on my database. I did a test with my friend and when I sent him the link to my website, he was able to see the appointments I had put there.

## Recover all appointments

This endpoint recover the complete list of appointments stored in the database

URL (Endpoint)

- http://localhost/Database/Appointment/recover_appointment.php

Request Method

- GET ( Because all I need to do is read the data stored in my database, and make no changes. I just recover everything )

Arguments

- None 

Return Value

- A JSON table containing all appointments

- http://localhost/Database/Appointment/recover_appointment.php

Proof of Execution

---

- JSON file created

Menu

---

- In PHP MyAdmin

Menu

---

- On the website

Menu

---

## Insert appointment

This endpoint allows you to add an appointment to the database

URL (Endpoint)

- http://localhost/Database/Appointment/insert_appointment.php

Request Method

- POST ( Because I need it to send new data to my database )

Arguments

- task (string, required) -> Name of task

- date_hour (string - format YYYY-MM-DD HH:MM:SS, required) → Date and time of appointment

- device_id (integer, required) → ID of the device associated with the appointment

Warning : if an argument is missing, it will not work

Return Value

- This allows me to display in a JSON file only the last appointment that was added

- http://localhost/Database/Appointment/get_last_appointment.php

Proof of Execution

---

- Added from the website

Menu

---

- Only the last added displayed

- http://localhost/Database/Appointment/get_last_appointment.php

Menu

---

- All appointments displayed

- http://localhost/Database/Appointment/recover_appointment.php

Menu

---

## Edit appointment

This endpoint allows you to edit an appointment to the database

URL (Endpoint)

- http://localhost/Database/Appointment/update_appointment.php

Request Method

- POST ( I know there's a PUT option for modifying data, but I prefer to stick with POST because the result is the same: I can modify data )

Arguments

- appointment_id (integer, required) → The ID of the appointment

- task (string, required) -> Name of task

- date_hour (string - format YYYY-MM-DD HH:MM:SS, required) → Date and time of appointment

Warning : if an argument is missing, it will not work

Return Value

- This allows me to display in a JSON file only the last appointment that was updated

- http://localhost/Database/Appointment/get_last_updated_appointment.php

Proof of Execution

---

- Edited from the website

Menu

---

- Only the last edited displayed

- http://localhost/Database/Appointment/get_last_updated_appointment.php

Menu

---

- Only the last added displayed ( no changement here )

- http://localhost/Database/Appointment/get_last_appointment.php

Menu

---

- All appointments displayed

- http://localhost/Database/Appointment/recover_appointment.php

Menu

---

## Delete appointment

This endpoint allows you to edit an appointment to the database

URL (Endpoint)

- http://localhost/Database/Appointment/delete_appointment.php

Request Method

- POST ( I know there's a PUT option for modifying data, but I prefer to stick with POST because the result is the same: I can modify data )

Arguments

- appointment_id (integer, required) → The ID of the appointment

Warning : if an argument is missing, it will not work

Return Value

- This allows me to display in a JSON file only the last appointment that was deleted

- http://localhost/Database/Appointment/get_last_deleted_appointment.php

Proof of Execution

---

- Deleted from the website

---

- Only the last edited displayed ( no changement here )

- http://localhost/Database/Appointment/get_last_updated_appointment.php

---

- Only the last added displayed ( no changement here )

- http://localhost/Database/Appointment/get_last_appointment.php

---

- All appointments displayed

- http://localhost/Database/Appointment/recover_appointment.php

---

## If we deleted the last add

---

- Deleted from the website

---

- Only the last edited displayed ( no changement here )

- http://localhost/Database/Appointment/get_last_updated_appointment.php

---

- If the last appointment is deleted, you're back to the one before 

- http://localhost/Database/Appointment/get_last_appointment.php

---

- All appointments displayed

- http://localhost/Database/Appointment/recover_appointment.php

The REST API documentation explains the input, output, and endpoint URL for each API to help you use them effectively.

---

There is a full explanation of the used technology.

---

All the design choices are explained in detail of the front-end and back-end of the web application.

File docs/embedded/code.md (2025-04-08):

# Embedded code

This is not a place to put your code, but to describe the code that you have written. You can describe the code in a general way, but also go into detail on specific parts of the code. You can also refer to the code in your repository. So just add a link to the code in your repository.

---

This program, entitled ESP32, controls a connected smart calendar. It uses an LCD screen, a 7-segment display, a servo-motor, a DFPlayer audio module, sensors (button, LDR, PIR), and connects to Wi-Fi to retrieve appointments from an external API. It manages event display, user interaction (button and motion detection), time synchronization via NTP, and an embedded web server for remote interaction.

**Link to the main code on GitLab**: [Victor HOEGY](https://gitlab.fdmci.hva.nl/IoT/2024-2025-semester-2/individual-project/buudiizaaduu29/-/blob/main/Victor/Arduino/ESP32/Final/ESP32.ino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)

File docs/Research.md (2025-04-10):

# Research to Market

## Introduction / Context :

The daily use of calendars and reminder tools is often repetitive and not very engaging. To respond to this monotony, this research is part of a functional and experiential improvement of a connected calendar inspired by the Warhammer 40,000 universe. This project aims to integrate visual and audio interactive elements to enhance user engagement and offer an immersive experience.

The main target of this project is fans of the Warhammer 40,000 universe, a global community estimated between 30 and 50 million people. The dense and rich narrative universe of Warhammer allows for aesthetic and functional integration into everyday objects. The project thus proposes an original alternative to the standard reminder: personalized voice interactions, thematic aesthetics, and automatic audio activations triggered by user presence.

---

## Research question :

What front-end tools are currently available ?

## Sub-questions :

How can the chosen tool be used to integrate interactive elements easly ?

---

## Research method :

To answer the research question, a fairly simple method was used: an online literature review to compare the best-known front-end development tools. The goal was to find tools that could improve a website's visual style and allow the addition of interactions such as sound or animation.

The steps were as follows:

First, list the most commonly used tools such as React, Vue, Angular, Vanilla JS, or Svelte

Then, check their official documentation to see what features they offer

Read recent comparative articles written by developers to better understand the pros and cons of each

Check whether they make it easy to add styles, sounds, animations, or visual effects

Finally, look at how easy these tools are to use and how well they are explained online

Even if this method is not complex, it gives a clear and honest overview of what exists today to improve a modern and dynamic web interface.

---

## Results

The research helped to better understand what each tool offers. An article titled [Comparing Angular, React, Vue, and Vanilla-JS](https://dev.to/rfornal/comparing-angular-react-vue-and-vanilla-js-37o9)  helped sort out the best-known frameworks.

React is very complete, well-documented, with lots of tutorials and a large community. It also allows you to easily add animations, sound, or visual effects.

Vue.js is easier to start with, but the community is slightly smaller, which can sometimes make finding help a bit harder.

Angular is very powerful but mostly used in large professional projects. It’s a bit more complicated to learn.

Vanilla JS is useful for small tasks, but not sufficient to handle a visually advanced project.

Another article, [Introducing Svelte, and Comparing Svelte with React and Vue](https://joshcollinsworth.com/blog/introducing-svelte-comparing-with-react-vue), presents Svelte as a simple, efficient, and fast-to-use tool. It requires little code, is close to the HTML/CSS we already know, and simplifies component management. Its community is smaller than React’s, but this does not pose much of a problem for this type of project.

---

## Implementation

After choosing which tool I was going to use to improve my front-end, I thought long and hard about what I could improve or add. I reread my website and asked myself, if I were a person who knew nothing about Warhammer 40k, what elements would I like to have for a little more explanation ? I first wrote my explanatory text to find out more about Omnissiah and techpriests. Then I was thinking, okay, I've got the text, but how do I add my text to my website? I started thinking, well, in Space Marine 2, in the campaign, there's a computer that explains the purpose of our first mission, and I really liked the animations on it, except that I'm not a professional developer, so I made it look like it's an Astra Militarum terminal, I had to add a few more lines to make it look like someone was trying to connect to it, so I'll let you see what I've implemented in the video.

**Proof 1**: [See the first proof](./proof1.mp4)  

Concerning the 2nd page, I thought that everything was more or less explained, so why not concentrate on my 3D model? It's true that when you look at my 3D model, you can ask yourself various questions: what does the PIR sensor, the button and the photoresistor do? That's why I've explained everything, and what's more, I've succeeded with great difficulty in implementing my 3D model with the ability to rotate it to show it from all angles ! 

**Proof 2**: [See the second proof](./proof2.mp4)  

---

## Code

Display the terminal **with** Svelte :

```html
<div id="omnissiah-overlay" class="hidden fixed inset-0 bg-black bg-opacity-90 backdrop-blur-sm z-50 flex items-center justify-center">
  <div class="terminal_svelte text-green-400 font-mono p-6 rounded-lg max-w-xl w-full mx-4 border border-green-500 shadow-xl animate-popup relative overflow-hidden">
    ...
  </div>
</div>
```

Display the terminal **without** Svelte :

```html
<!-- HTML -->
<div id="omnissiah-overlay" class="hidden fixed inset-0 bg-black bg-opacity-90 backdrop-blur-sm z-50 flex items-center justify-center">
  <div class="text-green-400 font-mono p-6 rounded-lg max-w-xl w-full mx-4 border border-green-500 shadow-xl relative overflow-hidden">
    
    <!-- Spinning gear icon -->
    <div class="absolute top-4 right-6 animate-spin text-green-500">⚙️</div>

    <!-- Terminal heading -->
    <h2 class="text-lg font-bold mb-4">[ Astra Militarum Transmission Terminal ]</h2>

    <!-- Dynamic terminal text output -->
    <div id="terminal-text" class="whitespace-pre-line text-green-300 text-sm leading-relaxed">
      Accessing data logs... \n Omnissiah protocol initiated...
    </div>
    <span class="inline-block w-2 h-4 bg-green-400 animate-pulse mt-2"></span>

    <!-- Terminal loading bar -->

    <!-- Close button -->
    <div class="text-right mt-6">
      <button onclick="closeOverlay()" class="bg-green-700 hover:bg-green-600 text-white py-2 px-4 rounded">OK</button>
    </div>
  </div>
</div>

<!-- Button to toggle terminal -->
<button onclick="openOverlay()" class="fixed bottom-6 right-6 bg-red-900 text-white px-4 py-2 rounded z-50">Who is the Omnissiah ?</button>

<!-- JS -->
<script>
  function openOverlay() {
    document.getElementById("omnissiah-overlay").classList.remove("hidden");
    document.getElementById("terminal-loading").style.width = "100%";
  }

  function closeOverlay() {
    document.getElementById("omnissiah-overlay").classList.add("hidden");
    document.getElementById("terminal-loading").style.width = "0";
  }
</script>
```

Display the 3D model and the Animation text **with** Svelte :

```html
<script>
  import { onMount } from 'svelte';
  let visible = false;

  let text = 'Tactical interface loaded.\nOmnissiah protocol active.';
  let display = '';
  let i = 0;

  function toggleViewer() {
    visible = !visible;
    if (visible) {
      display = '';
      i = 0;
      decrypt();
    }
  }

  function decrypt() {
    const interval = setInterval(() => {
      if (i < text.length) {
        display += text[i];
        i++;
      } else {
        clearInterval(interval);
      }
    }, 35);
  }

  onMount(() => {
  });
</script>

<button on:click={toggleViewer}>Inspect Model</button>
```

Display the 3D model and the Animation text **without** Svelte :

```html
<button onclick="openViewer()">Inspect Model</button>

<!-- 3D container + encrypted text -->
<div id="viewer" style="display:none;">

  <button onclick="closeViewer()">Close</button>
</div>

<!-- BASIC JS -->
<script src="https://cdn.jsdelivr.net/npm/three@0.141.0/build/three.min.js"></script>
<script src="https://cdn.jsdelivr.net/npm/three@0.141.0/examples/js/loaders/STLLoader.js"></script>

<script>
  let scene, camera, renderer, mesh;

  function openViewer() {
    document.getElementById('viewer').style.display = 'block';
    initViewer();
    startDecryptAnimation();
  }

  function closeViewer() {
    document.getElementById('viewer').style.display = 'none';
  }

  function initViewer() {
    const container = document.getElementById('model-viewer');
    container.innerHTML = '';

    scene = new THREE.Scene();
    camera = new THREE.PerspectiveCamera(75, 1, 0.1, 1000);
    camera.position.set(100, 100, 100);
    camera.lookAt(0, 0, 0);

    renderer = new THREE.WebGLRenderer({ alpha: true });
    renderer.setSize(500, 500);
    container.appendChild(renderer.domElement);

    const loader = new THREE.STLLoader();
    loader.load('/models/your_model.stl', function (geometry) {
      const material = new THREE.MeshNormalMaterial();
      mesh = new THREE.Mesh(geometry, material);
      mesh.rotation.set(-Math.PI / 2, 0, 0);
      scene.add(mesh);
    });

    animate();
  }

  function animate() {
    requestAnimationFrame(animate);
    if (mesh) mesh.rotation.z += 0.005;
    renderer.render(scene, camera);
  }

  function startDecryptAnimation() {
    const el = document.querySelector('.decrypt-text');
    const original = el.dataset.text;
    let display = Array.from(original).map(() => ' ');
    let i = 0;
    el.style.opacity = 1;

    const interval = setInterval(() => {
      for (let j = i; j < original.length; j++) {
        display[j] = Math.random() > 0.5 ? String.fromCharCode(33 + Math.random() * 94) : display[j];
      }
      el.innerText = display.join('');
      display[i] = original[i];
      i++;
      if (i >= original.length) {
        el.innerText = original;
        clearInterval(interval);
      }
    }, 35);
  }
</script>

```

---

## Conclusion

In the end, even though React is very complete and widely used in development, Svelte seems more suitable for a personal or educational project. It is easier to use, quicker to set up, and allows for adding animations or styling without too much code. For this project, Svelte is a good match for the needs.

---
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

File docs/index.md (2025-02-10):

# Blueprint name here

Describe the purpose of your blueprint. Design a nice front-page image that will describe your product.

The aim of my blueprint is to transform a cuckoo clock into a smart calendar, so that users can enter their appointments themselves from a website. As for the bird part, I'd like to turn it into a commissar so that it ties in with the design I'd like to do. Instead of hearing a
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

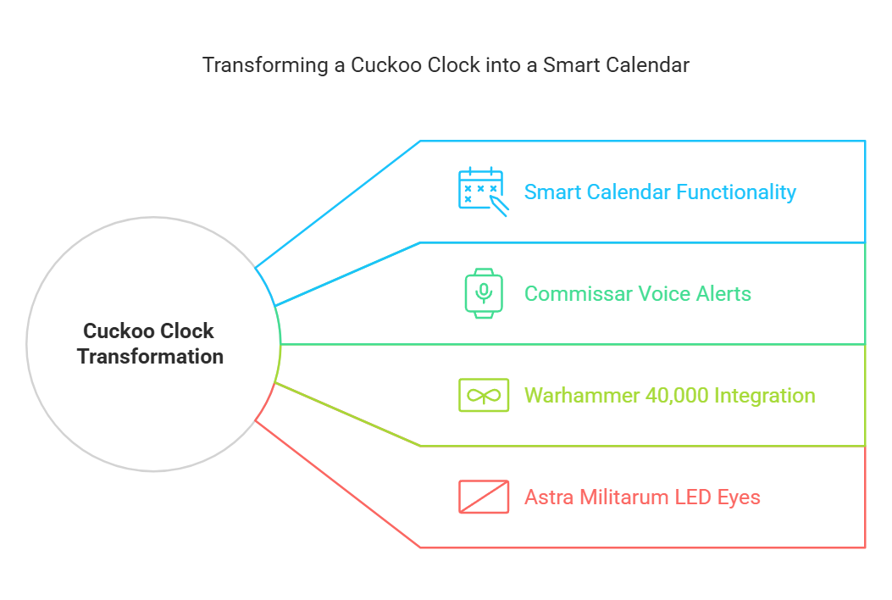
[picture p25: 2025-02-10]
docs/Blueprint_IoT_Students_Portfolio_index.png.png

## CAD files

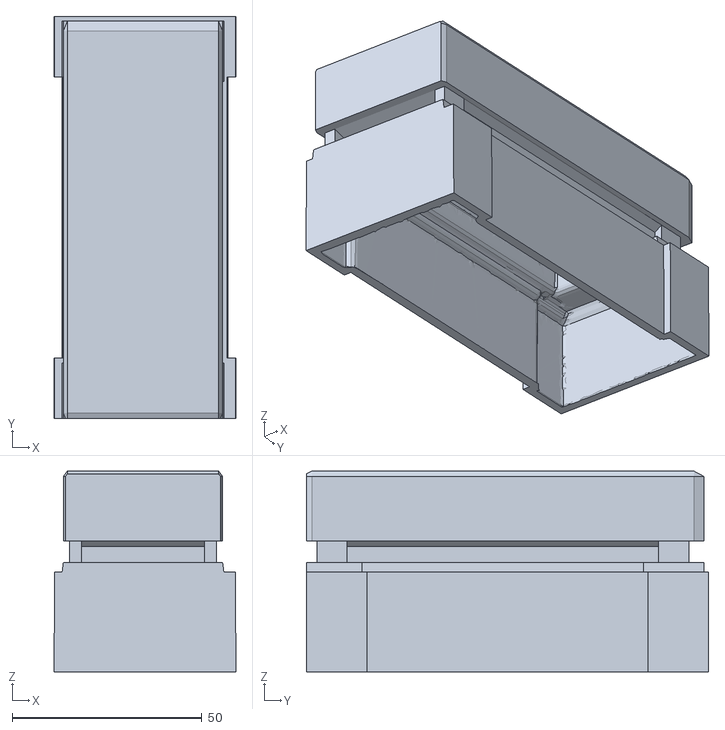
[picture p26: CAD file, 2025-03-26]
docs/uxd/3D Model/Step222.stl
48.0 x 106.0 x 53.0

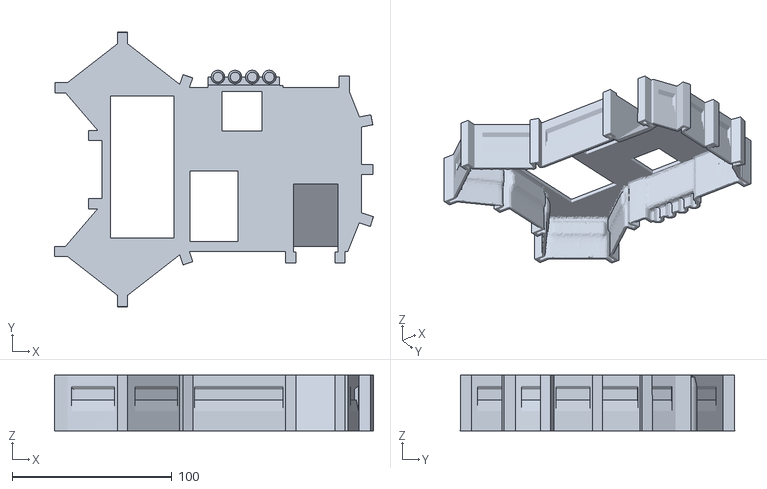
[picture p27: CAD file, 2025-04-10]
docs/uxd/Create/Base.stl
200.0 x 172.1 x 35.0

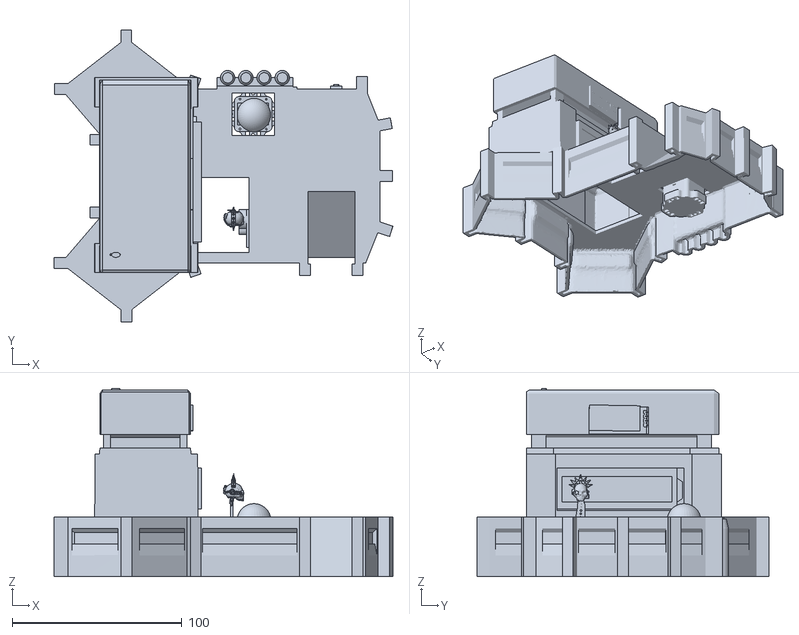
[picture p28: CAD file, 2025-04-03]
omnissiah-info/public/models/Astra_Militarum_Explication.stl
200.0 x 172.1 x 111.0

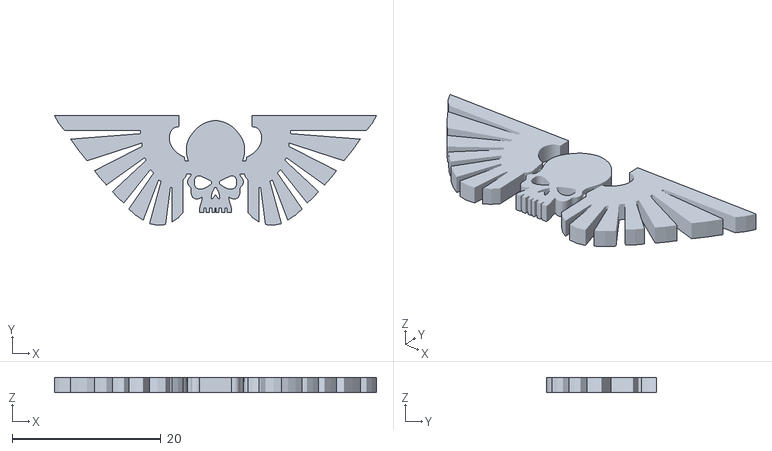
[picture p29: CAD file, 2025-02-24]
Victor/3D model/Astra Militarum Emblem4.stl
43.4 x 14.8 x 2.00

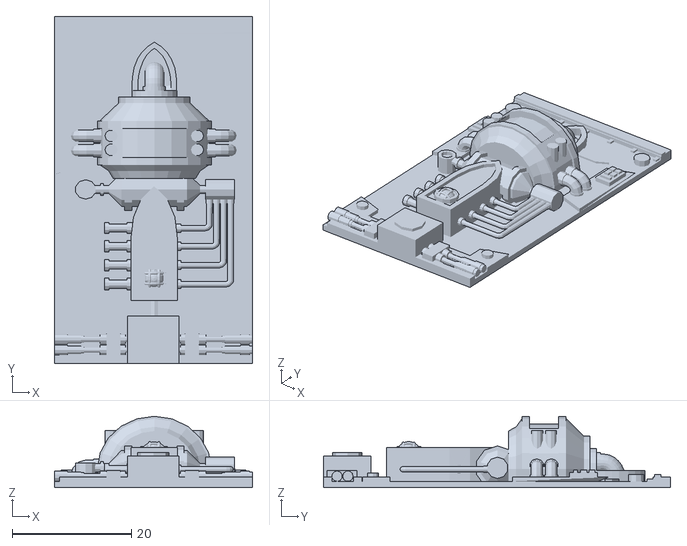
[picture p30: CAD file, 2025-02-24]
Victor/3D model/Box/manufactorum_wall_piece_3.stl
33.3 x 58.3 x 12.0

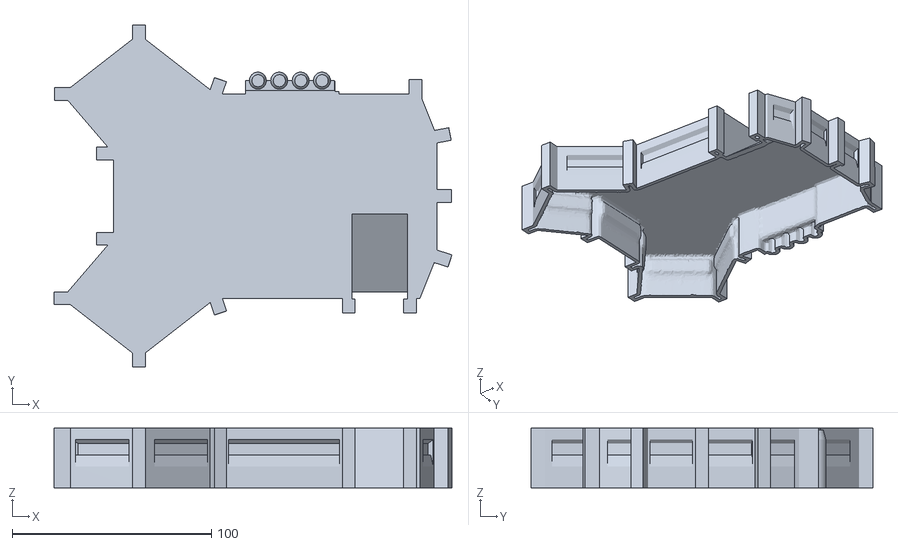
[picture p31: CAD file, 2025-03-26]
docs/uxd/3D Model/Step2222.stl
200.0 x 172.1 x 30.0

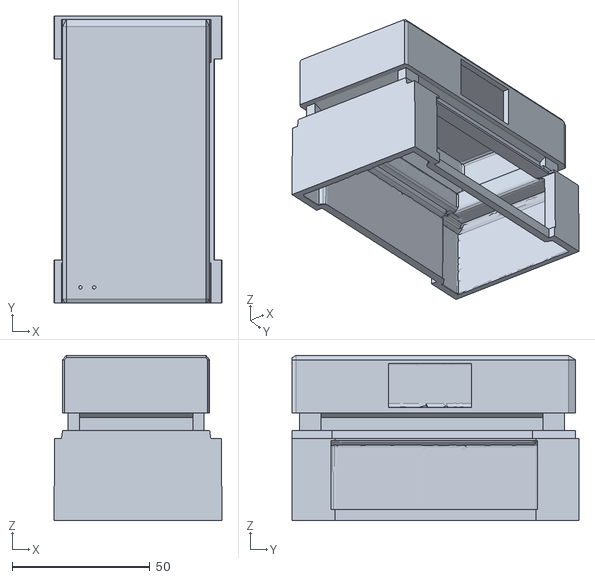
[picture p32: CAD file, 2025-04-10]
docs/uxd/Create/Tour.stl
61.0 x 104.0 x 60.0

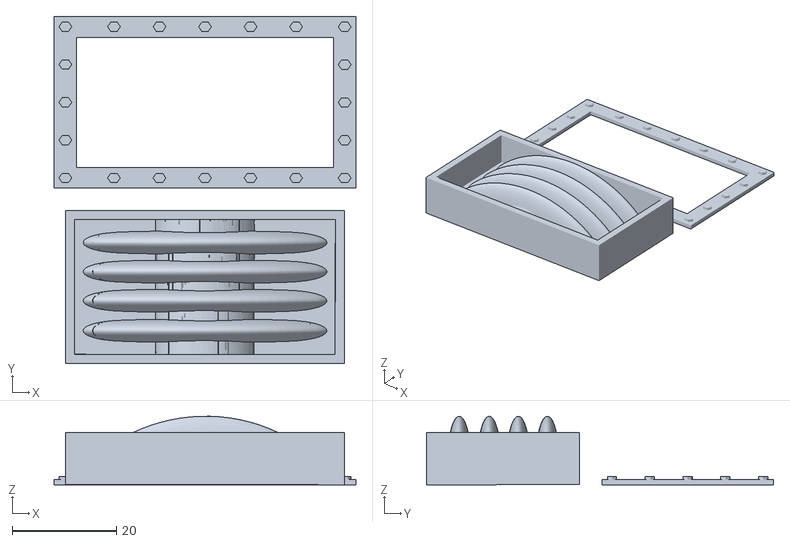
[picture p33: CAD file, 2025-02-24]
Victor/3D model/Box/manufactorum_wall_piece_5.stl
58.0 x 66.7 x 13.2

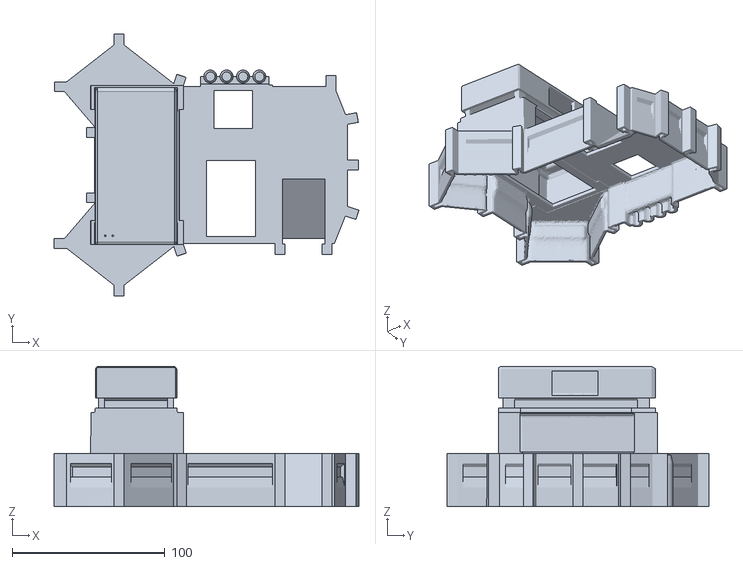
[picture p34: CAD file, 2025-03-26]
docs/uxd/3D Model/Last.stl
200.0 x 172.1 x 92.0

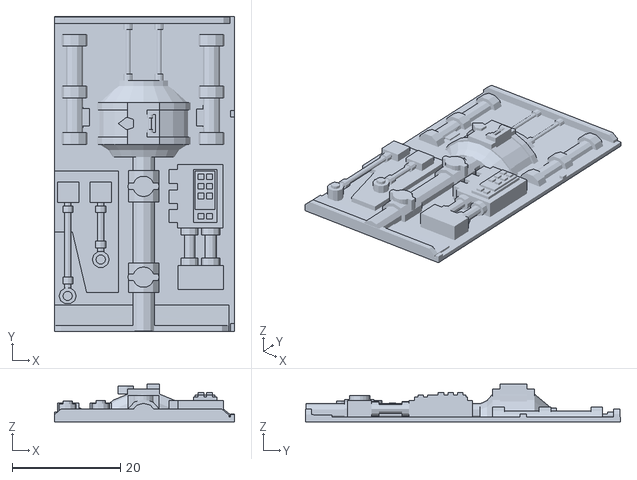
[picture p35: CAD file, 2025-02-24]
Victor/3D model/Box/manufactorum_wall_piece_2.stl
33.3 x 58.3 x 7.00

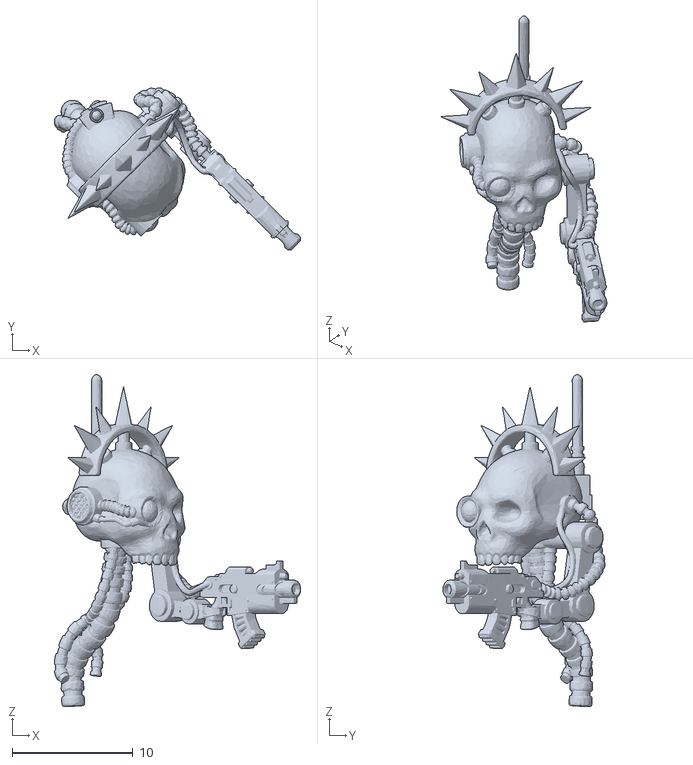
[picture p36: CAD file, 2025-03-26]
docs/uxd/3D Model/Cuckoo.stl
20.4 x 13.4 x 27.5

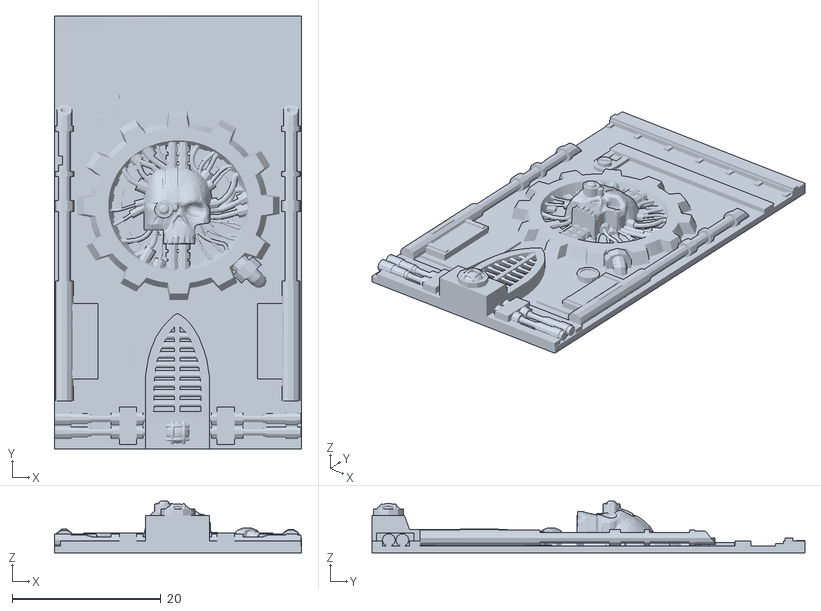
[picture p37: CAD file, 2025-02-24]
Victor/3D model/Box/manufactorum_wall_piece_1.stl
33.3 x 58.3 x 7.00

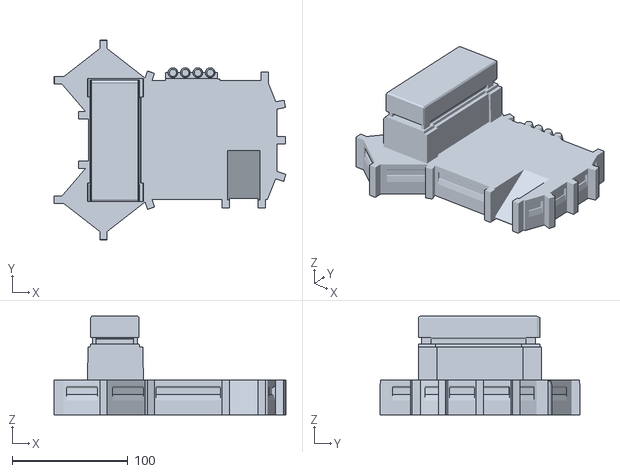
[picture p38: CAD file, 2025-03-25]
docs/uxd/3D Model/Step19.stl
200.0 x 172.1 x 85.0

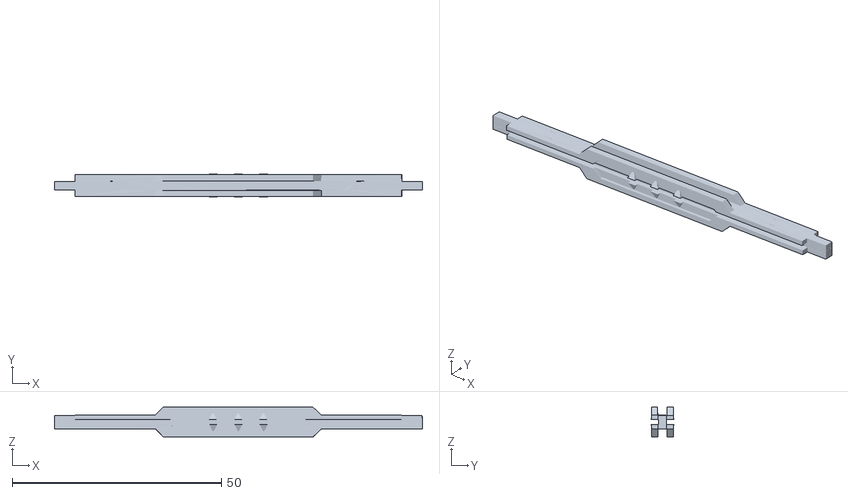
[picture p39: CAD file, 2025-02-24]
Victor/3D model/Box/Top_brace.stl
88.0 x 5.60 x 7.15

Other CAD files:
docs/uxd/3D Model/Step18.stl
Victor/3D model/Box/Column_peg.stl
docs/uxd/3D Model/Step10.stl
Victor/3D model/Box/Top_flat_brace.stl
Victor/3D model/Box/Wall_6.stl
docs/uxd/3D Model/Step2.stl
docs/uxd/3D Model/Step4.stl
docs/uxd/3D Model/Step6.stl
docs/uxd/3D Model/Step8.stl
docs/uxd/3D Model/Step9.stl

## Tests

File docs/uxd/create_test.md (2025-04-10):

# Create & Test

Write here your own content!

## DIGITAL MANUFACTURING

The print was carried out using an Ultimaker 2+ Connect, equipped with a 0.4 mm nozzle. The filament used is grey PLA, 1.75 mm in diameter, chosen for its ease of use, stable behavior without a heated enclosure, and perfect compatibility with fast printing settings. PLA has the advantage of limiting warping and allows for higher print speeds than ABS or PETG, while remaining biodegradable under industrial composting conditions.

## PLA Specifications:

Density : ~1.24 g/cm³

Glass transition temperature : ~60°C

Melting temperature : 180–220°C

Tensile strength : ~37 MPa

Elongation at break : ~6%

Printing settings used (Ultimaker Cura)

Layer height : 0.1 mm

Wall thickness : 3 wall lines

Infill : 20% (Gyroid pattern)

Print speed : 50 mm/s

Nozzle temperature : 200°C

Bed temperature : 60°C

Cooling : fan at 100%

Supports : enabled, placed everywhere, overhang angle at 50°, horizontal expansion 0.8 mm

## Optimisations

## Quality

Layer Height **0.15 mm**

---

## Walls

Wall Thickness **0.8 mm**

Wall Line Count **2**

Horizontal Expansion **-0.015 mm**

---

## Top / Bottom

Top / Bottom Thickness **0.75 mm**

Top Layers **5**

Bottom Layers **5**

---

## Infill

Infill Density **20 %**

Infill Pattern **Grid**

---

## Material 

Printing Temperature **210.0 °C**

Build Plate Temperature **60 °C**

---

## Speed

Print Speed **60.0 mm/s**

---

## Support

Support Structure **Normal**

Support Placement **Everywhere**

Support Overhang Angle **50.0 °**

Support horizontal Expansion **0.8 mm**

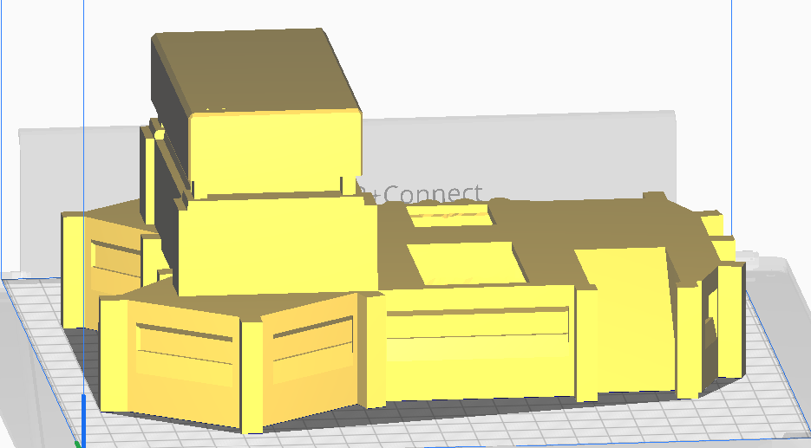
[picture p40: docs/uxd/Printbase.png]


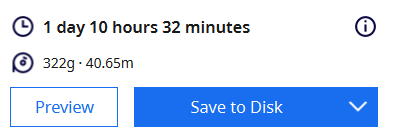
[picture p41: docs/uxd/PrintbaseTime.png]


---

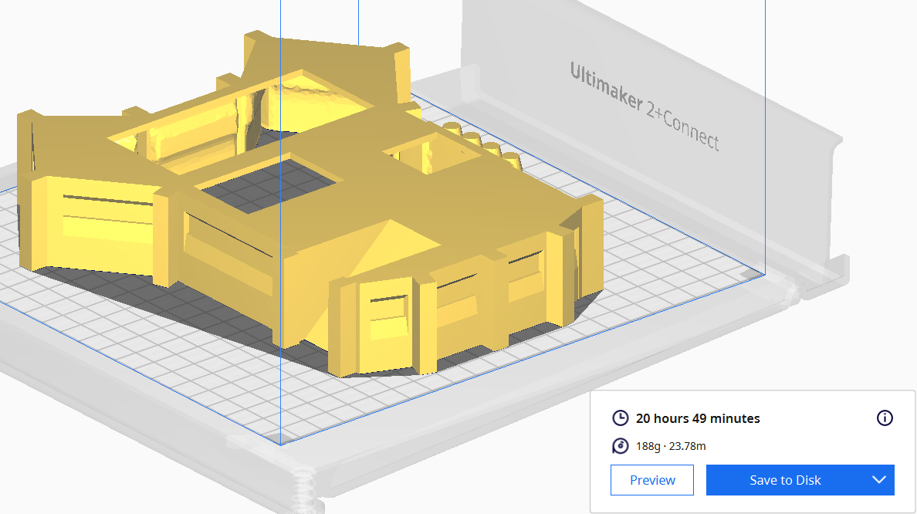
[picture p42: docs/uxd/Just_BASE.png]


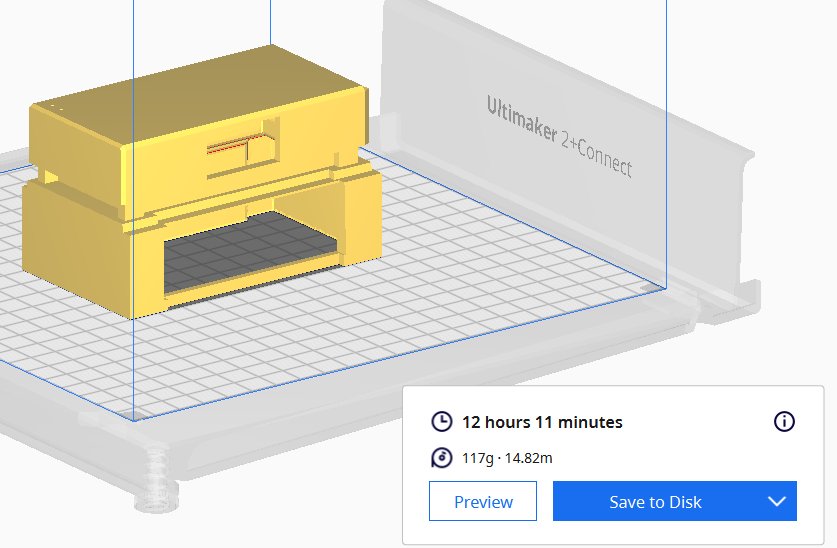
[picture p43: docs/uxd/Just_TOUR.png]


When I split them, I reduce the time by **1h41**

---

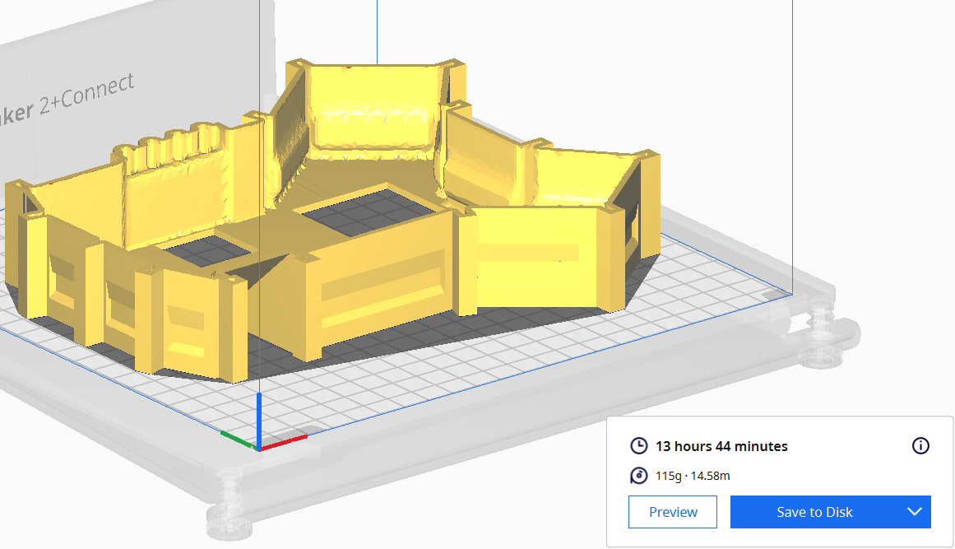
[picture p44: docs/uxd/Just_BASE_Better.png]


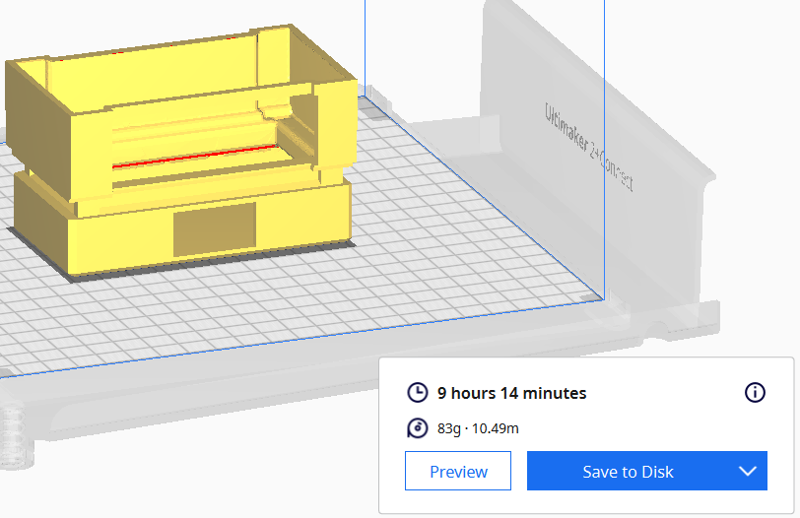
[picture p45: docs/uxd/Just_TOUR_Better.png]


[Files on GitLab](https://gitlab.fdmci.hva.nl/IoT/2024-2025-semester-2/individual-project/buudiizaaduu29/-/tree/main/docs/uxd/Create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)

But when I flip them I reduce the time by **11 hours and 34 minutes !**

---

## Manufacturing

The first step is to fit the servo motor and the pir sensor

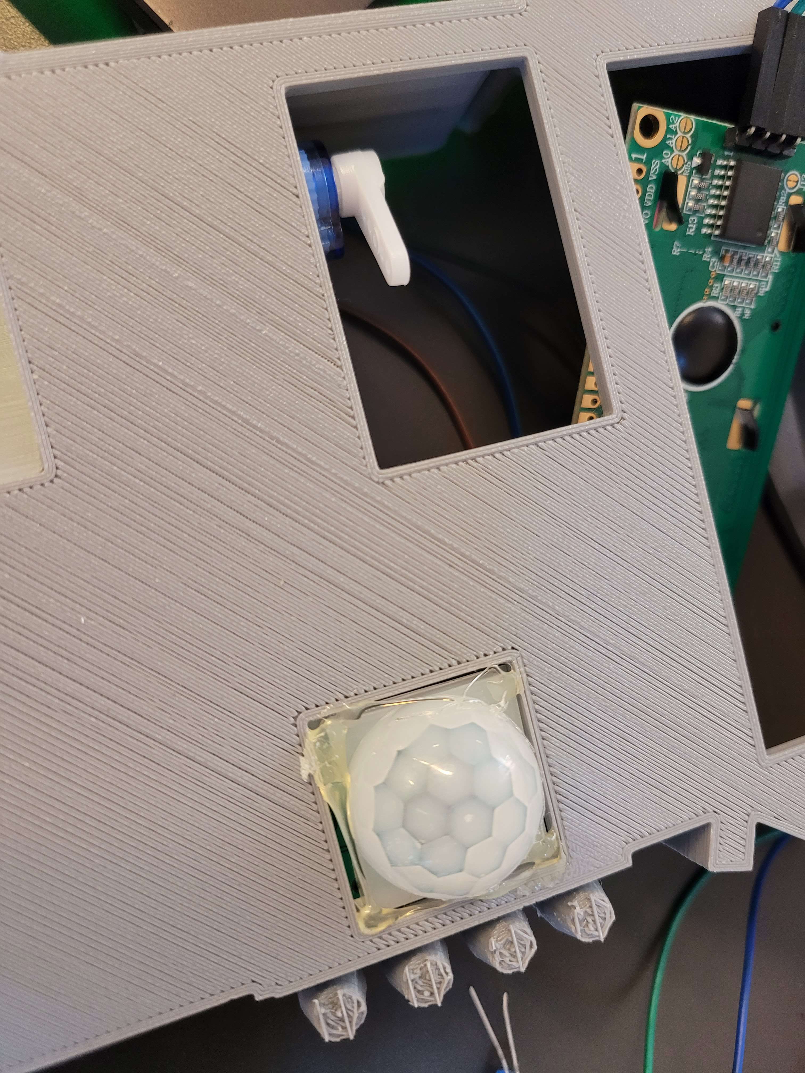
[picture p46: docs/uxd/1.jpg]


Then we take care of the button

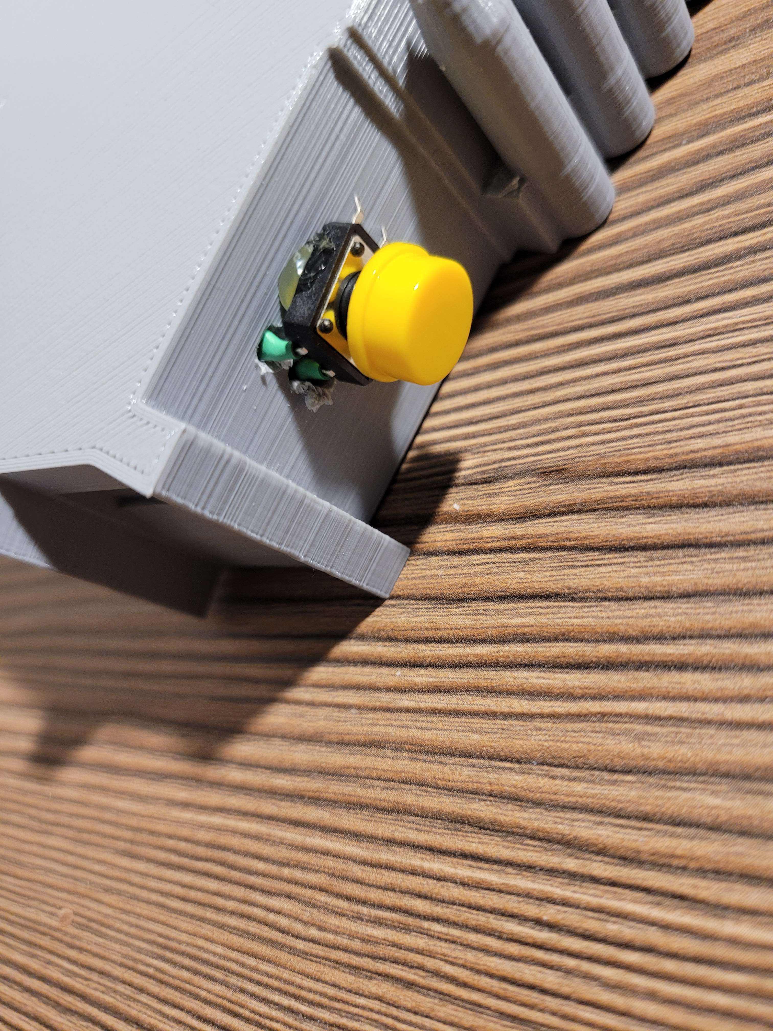
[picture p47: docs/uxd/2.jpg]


We'll take care of the 7 segments

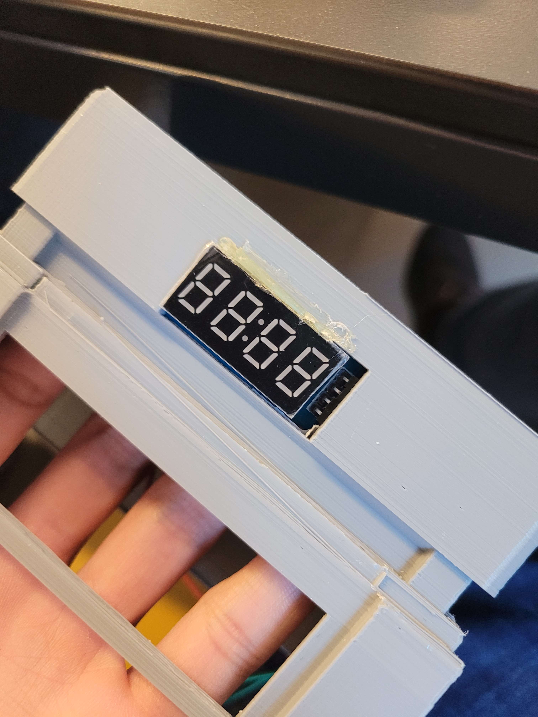
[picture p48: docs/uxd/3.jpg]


We'll take care of the LCD screen and the photo resistance

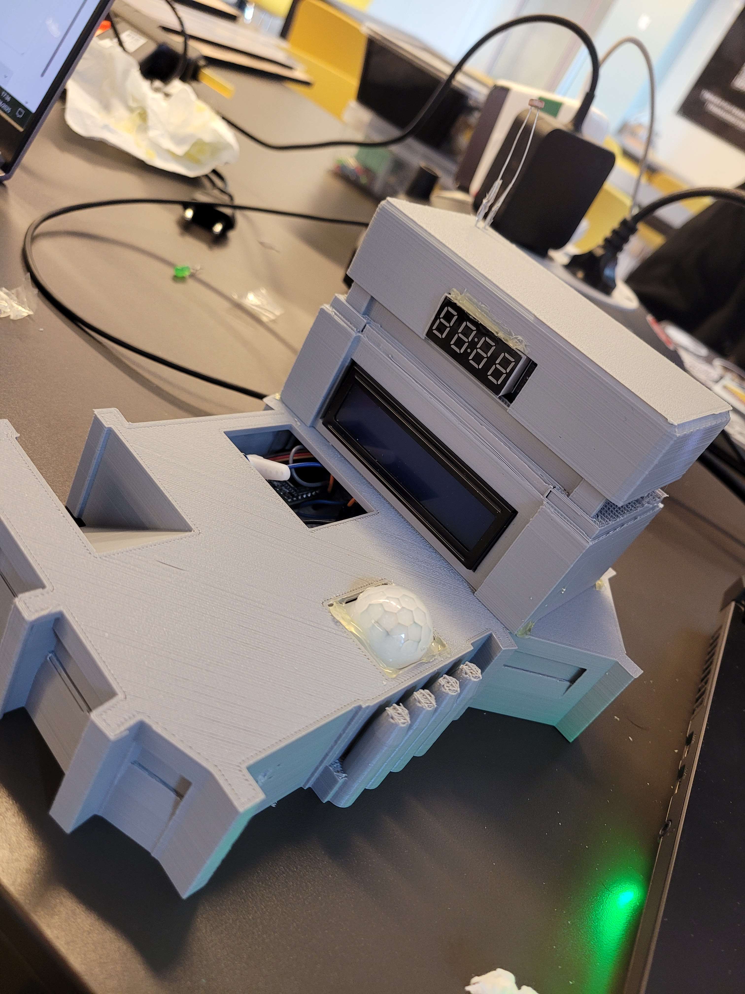
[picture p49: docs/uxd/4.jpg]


We take care about the jumper wires we stick together 

Menu

And we hang the flag

Menu

## User Test

**Objective**

Evaluate the usability, clarity, and functionality of the Warhammer-themed smart calendar’s web interface, focusing on ease of adding/modifying appointments and immersive user feedback (audio/visual).

**Test Scenarios**

## Appointment Creation Flow

**Objective:** Ensure the user can create and modify an appointment intuitively and quickly.  

**Steps:**

- Access the website homepage.
- Click on the "Log Your Sacred Duty" button.
- Add an appointment with title and time.
- Try modifying it right after.

**Expected Outcome :**  

The task should be completed in under 20 seconds without assistance, and the user should feel guided throughout.

**Result :**

Most users completed the action smoothly, but a few were confused by the color and position of the “Delete” and “Modify” buttons.

---

## Immersion

**Objective:** Assess whether Warhammer 40K fans feel immersed by the sounds and visuals. 

**Stepsc:**

- Trigger the voice line and animation by adding a task.
- Hover over or interact with thematic icons and elements.

**Expected Outcomec:**  

Fans should recognize and appreciate the Warhammer-themed feedback. Non-fans should still find the experience visually and auditorily engaging.

**Resultc:**  

Fans loved the aesthetic and voice effects. Non-fans found it “unique” but some suggested more guidance to understand the context.

---

## Interface Clarity

**Objective:** Measure how clearly the interface communicates each function.  

**Steps:**

- Try deleting or editing an existing appointment.
- See if the buttons and color scheme are intuitive.
- Try using the system without prior explanation.

**Expected Outcome:** 

Users should not accidentally delete an appointment or get confused during the edit process.

**Result:**  

Several users found the “Delete” button too close to the “Edit” one, creating hesitation. Colors weren’t always intuitive (e.g., Cancel and Confirm looked similar).

---

## Feedback Collection

**Method:** short interviews 

**Participants:** 6 users (3 Warhammer fans, 3 non-fans)  

**Key Questions:**

- Was the interface intuitive ?
- Did you enjoy the Warhammer visuals ?
- Did you face any confusion when editing appointments?
- Would you use such a calendar in daily life ?
- Suggestions for improvement ?

---

## Success Metrics

- **≥4/5 average rating** on usability and thematic satisfaction  
- **≤1 user out of 6** experiencing blocking confusion  
- **Average task time** < 20 seconds to add or edit a task  

---

## Test Results

| **Question** | **Average Score (out of 5)** |
|---|---|
| Was the interface intuitive to use ? | 4.2 |
| Were the visuals/sounds enjoyable ? | 4.8 |
| Did you understand what each button did ? | 3.5 |
| Would you use such a product regularly ? | 3.3 |

**Suggestions for Improvement :**

- Change the color of Cancel/Modify/Delete buttons
- Remove the “Delete” option during editing

---

## Optimisations Based on Feedback

**Changed button colors** to make Cancel/Modify/Delete clearer  
**Disabled "Delete" during edit mode** to reduce errors  

```js
function ism_editAppointment(appointment_id, currentTitle, currentDateTime) {
  document.querySelectorAll('.ism-edit-form').forEach(form => form.remove());

  document.querySelectorAll('.ism-edit-button, .ism-delete-button').forEach(btn => {
    btn.style.display = 'inline-block';
  });

  const appointmentDiv = document.querySelector(`[data-id='${appointment_id}']`);
  if (!appointmentDiv) {
    console.error("L'élément avec l'ID donné n'a pas été trouvé");
    return;
  }

  appointmentDiv.querySelectorAll('.ism-edit-button, .ism-delete-button').forEach(btn => {
    btn.style.display = 'none';
  });

  const editForm = document.createElement("div");
  editForm.classList.add("ism-edit-form");
  editForm.style.marginTop = "1rem";

  editForm.innerHTML = `
    <label>Edit title:</label>
    <input type="text" id="ism-edit-title" value="${currentTitle}">
    <label>Change date and time:</label>
    <input type="datetime-local" id="ism-edit-datetime" value="${currentDateTime}">
    <button onclick="ism_saveEditedAppointment(${appointment_id})">Save</button>
    <button onclick="this.closest('.ism-edit-form').remove(); ism_loadAppointments();">Cancel</button>
  `;

  appointmentDiv.appendChild(editForm);
}
```

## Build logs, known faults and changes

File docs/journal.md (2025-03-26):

# Learning journal

Your learning journal can be seen as a diary of your learning process. It is a place where you can reflect on your learning, and where you can keep track of your progress. It is also a place where you can keep track of your questions, and where you can write down your answers to those questions.

So for example when you receive feedback on your project, you can write down the feedback and your reflection on it in your learning journal. You can also write down what you have learned from the feedback, and how you will apply it in your project.

## Eighth week

### Wenesday 26/03

Today, I was finally able to 3D print my servo-skull, which will serve as the cuckoo in my project. After inspecting the result, I made the final modifications, including adjusting the holes for the final assembly. This step allowed me to be sure that all the parts would fit together perfectly during assembly.

At the same time, I updated my Fritzing diagram. This took some time, as I wanted to be precise to avoid any confusion in the next steps. From now on, my diagram accurately reflects all the real connections in the project.

### Tuesday 25/03

Today I devoted my entire day to making progress on the code part of my project. Above all, I wanted to make sure that all the components interacted correctly with the ESP32.

I started by reviewing the physical connections in detail, checking one by one which pins were used for each component. Once I was sure that everything was properly connected, I initialized all my components: the LCD screen correctly configured, the DFPlayer module managing all sound effects, and the time display on the 7-segment module. Next, I integrated precise time synchronization using the NTP protocol, ensuring that my system always had the correct time.

I had a few problems with the WiFi connection, including intermittent disconnections. To resolve this, I added automatic reconnection logic to my code every second in the event of WiFi signal loss. I also added display messages on the LCD screen to inform the user of the connection status.

Much of my work today focused on dynamic appointment management. I coded a routine that allows the ESP32 to regularly (every 5 seconds) retrieve appointments from my API. These appointments are then clearly displayed on the LCD screen with date, time and label. To enhance user interaction, I programmed a sound feature with the DFPlayer: a specific sound is triggered each time an appointment is added, modified or deleted.

As far as sensor management is concerned, I've set up a “night mode” logic controlled by the photoresistor. As soon as ambient brightness falls below a certain predefined threshold, the system activates this mode, suspending all automatic sounds so as not to disturb during the night. When brightness rises above a second, slightly higher threshold, night mode is automatically deactivated and sounds resume as normal.

I've also added a function that plays a sound every hour on the hour, except when night mode is activated. This function uses the regular updating of the time by the NTP protocol.

Finally, I've refined the management of the PIR motion sensor to prevent unwanted triggering by adding a 5-minute time lock. This ensures that the system doesn't play motion detection sounds too often. 

### Monday 24/03

Today, I decided to concentrate fully on my 3D model. I knew I had a lot of work ahead of me to completely remake my model, so I preferred to clearly structure the steps I needed to take.

I started by taking precise measurements to ensure that the proportions were correct from the outset. This step took longer than expected, as I had to make several adjustments to ensure that everything corresponded perfectly to my references.

Next, I made the initial sketch directly on my modeling software. This part was pretty straightforward, but I did run into a few difficulties when it came to detailing specific parts of the model. I took my time to ensure that each element was well placed and proportioned.

Once the sketch was complete, I moved on to the actual modeling, step by step, working first on the general shapes before tackling the details. During this process, I had a few minor problems with the textures, particularly in achieving the effect I wanted on certain surfaces, but after several attempts, I finally found a satisfactory solution.

Towards the end of the day, I was able to start working on the fine details and decorative elements of the model.I haven't quite finished this stage yet, but I'm happy with the current result. 

---

## Seventh week

### Friday 21/03

My will weakens

### Thursday 20/03

Step 1 - 8 for the 3D Models

### Wenesday 19/03

Research part, Introduction, Research question, Sub question, Research method

### Tuesday 18/03

Today, I wanted to get down to the nitty-gritty of solving a problem I had encountered with the Wemos and the Arduino. Managing to launch a sound when a user adds, modifies or deletes an appointment. To say that it was easy would be a lie, because I've had my share of problems. First of all, I tried to connect my ESP32 to the Internet using the Wifi Manager, and all I could come up with was problems. For some reason, it kept reconnecting, even though I managed to retrieve the IP address to check if I was really connected, and I was so unsure that I started to doubt my connections - I thought I had too many components connected and that's why, for example, my DF Player Mini with its LCD screen kept rebooting. But no, my only problem was the wifi manager, but I'll have to deal with that later.
After that I had to sleep because I was tired, and since we don't have classes on Tuesday, I decided to keep working when I woke up. I continued my ESP32's code, I really want to have a sound when I add, edit or delete an appointment. Concerning my problems I fixed it all and now everthything is working now. I need to continue my code for display my differents appointment to my LCD screen.  

### Monday 17/03

Today I started my day planning what I was going to do for today, I knew I wanted to start the research part but I don't know where to start. So I took a few minutes to write down my schedule to be sure of what I was going to do today. After planning my day well, I read the different topics in relation to the research part, I admit that my initial choice was to want to do the Business part except that I remembered that I'm going to try to make a 3D model that comes from Games Workshop ( Warhammer 40,000 creators ) and then not to mention that all the voices line that I use comes from a game which is Dawn of War which also comes from Games Worshop so I knew that this part was screwed for me. When I read the Embedded Technology section, I didn't really want to do it, just like the User Interaction section. Since I don't have any cyber knowledge, I naturally chose the Web Application part. 

Once I'd chosen the topic that suited me best, I did my research into the different research methods. Given that in France we'd never done this before, it was a first for me, which is why choosing the Web part seemed the most affordable for me. Once I'd done my research, I started writing what I thought was relevant.

When I got home, I decided to take care of my embedded devices game once again. I'd already accepted that I'd have to pay for this defeat on my own, but I was determined to only pay for one. I started by looking up the ESP32 datasheet on the Internet, so as not to get the pins wrong.

I did the same as last time, I started by plugging in things I knew how to plug in without any problem, just the button to start with. What's really practical compared to ESP32 is that there was no need to make a lot of changes. 

I connected my photo resistor because I really wanted to connect all my inputs and then all my outputs. Same as the button, no great difficulty just that I was surprised that on the ESP32 it's not between 0 - 1023 but between 0 - 4095, that's why at the beginning when I saw ~2000 I was saying to myself that it's ok I've run my ESP32 already that this morning Mennos had succeeded for some reason that we all don't know in killing his Wemos. I was thinking I was rehashing the feat. But no, everything's working perfectly.

Since last time I hadn't managed to play a sound when a button was clicked, but it was a one-off, I wanted to see if I could play a sound when I pressed the button and I managed to do it, I was so happy to have succeeded ! That's why once I'd done that, I knew the rest would be much easier.

I connected the LEDs in such a way as to be able to switch them on when someone is standing in front of the smart calendar, while initiating a specific voice line. To do this, I used a PIR motion sensor to detect movement. I connected the sensor to the ESP32. Once the sensor detected a presence, the ESP32 triggered the corresponding LED to light up. Each time a movement was detected, a specific voice was launched by a connected loudspeaker.

I connected the 7-segment display to my ESP32, as it allowed the user to see the time. I used an RTC (Real-Time Clock) module to get the time. I wrote a function in my code to retrieve the current time and display it correctly for the 7-segment display.

I followed this up by connecting my 2 screens, one to display my heart rate and the other to display my appointments. For the heart rate display, I integrated a pulse sensor into the ESP32. I took over my code that allowed me to send analog signals representing a heart rate. The second screen, an LCD, was dedicated to appointments. It retrieved data from my database. The user interface was designed to be simple, so that upcoming appointments were clearly visible.

I also connected my servomotor. The servomotor has been integrated to move my commissar forward or backward, and will serve as a cuckoo clock.

I've added a note to my appointments so that I can perform a specific action when I decide to add, modify or delete an appointment. To do this, I first had to modify my database schema to add a note to an appointment, and I modified my database at the same time. To store the additional notes field, I updated my database schema by adding a new column to the appointments table. The “note” field allows me to add 3 small notes for my appointments that I'll use in my code. In addition, I modified my API endpoints to accept and return note data when retrieving appointment details. 

I've adapted my JavaScript code to work with what I've modified. To make the frontend reflect the new database structure, I updated my JavaScript code to handle the new notes function. These notes were then stored in the database and retrieved each time appointment data was retrieved. I also added event receivers to dynamically update the user interface when an appointment was modified or deleted. 

---

## Sixth week

## Friday 14/03

I failed, yesterday I couldn't do the programs I wanted to do, I had a lot of problems with the connection between the Arduino and the Wemos, I tried everything but I even got some help from Indigo who gave me some components to be able to do it, last week it was a Friday if I remember correctly he came to help me for more than 2 hours. I went over his Frietzing file with him, I went over his code with him and we modified everything, and even with that he told me that the configuration we'd managed to make was that only the wemos could send data, but that the arduino couldn't send any. In itself, I don't have a problem with that, because that's how I want it done.

That's why this week I've started all over again with my connection part, but I've found a solution which is just to buy an ESP32. Which I've done, I should receive it tomorrow, and as I'm going back to France today I'll be able to pick up the components I need. I ordered an LCD screen and an ESP32 for all my connections.

## Thursday 13/03

It's 3:00 AM as I write this leaning journal, I've been working on the part of the code that would allow me to control the connected outputs of my arduino board from my Wemos, but what I don't understand is why I can't do it. At first I thought it was a connection problem, but then I went back and reconnected what I thought was a potential problem. I ran tests to check every output without going through wemos because I thought it was a pin problem in the code or something.
The craziest thing is that it works, I can send data but I don't understand why I can only do it once, at least I know it's a code problem and not a problem with what I've plugged in.

I've got to get some sleep, I need to rest so I can work on finding the problem tomorrow, or at least in a few hours.

I spent a lot of hours trying to send specific data to my Arduino, but I don't know why it didn't work... I replaced my jumper wires. I tried to begin and restart all my programs to try to solve it, but even if I met a lot of problems, I know all my programs are working separately and the only solution I found is to buy an ESP32. I already received it but to my home. I did a lot of research to see if I could connect all my components to the ESP32 and, if I'm right, it should work because the problem with sending data to the Arduino from the Wemos will disappear. 

## Wenesday 12/03

On Monday I redid all my embedded devices, i.e. I started from scratch all my connections for my components, I completely rechanged all my inputs and outputs. It took me all day, but I did it. I'm not going to go into detail again, because I've already done that, but what I mean by that is that every day I have some kind of big “theme”.

Monday Embedded device

Tuesday Database

Wednesday Documentation

Thursday Code to communicate with the arduino via wemos

So today I went back to my System Architecture section and tried to add everything in it to keep it up to date, as our teacher had asked us to do. Hoping I've filled it in properly, I went back to my requirements documentation and added the latest components I've decided to use. For my embedded technical documentation, I rearranged everything to explain each component and the pins it uses. As for my technical documentation for the web part, I explained each page with what users can do. And for my database, I've added a criticism I noticed. 

### Tuesday 11/03

After finishing all the connection work, I started the day by working on my Database Schema. Today I wanted to finish all my database stuff, whether it was to be able to send, receive or delete data in my database. I'll go into more detail today. I wanted to modify some data on my Data Schema to make my life easier, whether to add or delete data, so I had to make the changes. For example, for the component names, I had set 255 when it wasn't really very consistent, so I modified my tables to ensure that there was a real dependency between the tables, e.g. if you delete the Sensor table, the SensorData table is automatically deleted because the sensor data depends on the sensors, and I did the same for the Device and Appointment tables.
Changes to the Database Schema inevitably mean changes to the ERD schema, and that's what I did, making the necessary changes to ensure consistency between the 2 schemas.

I wanted to start by adding my wemos to my database because in my schema it's my key component, if this component isn't there, the table doesn't exist and if this table doesn't exist nothing can be added, I wanted to check that my appointments were sending information to the wemos using the wemos ID and everything worked fine, I didn't need to make any changes.

After successfully connecting my wemos to my database, I had to send a first sensor to my database. I decided to use the button because it's really easy to use. Once I'd managed to connect my button to my database, I had to manage to send data to it, so I took the position of the button and made sure that as soon as the button was pressed, it was sent to the database. 

I'd already started yesterday, but I wanted to send data to my arduino board via my wemos, so I started with a simple test: manage to turn the LED on or off using the button connected to my wemos, which I managed to do easily and without too many problems. When I tried to do the same thing with the DF Player mini, it was immediately more complicated, because when I tried to send data to the arduino board, my DF Player mini was no longer detected at all. I carried out various tests and thought to myself that it was the DF Player that had blown up, so I had to run it unintentionally, and I'll have to buy another one. I ran a simple program just to launch an audio file on the SD card and it worked normally. I knew that the wemos could communicate with the arduino board because I was able to control the led with the button, I knew that the DF Player mini worked normally. There was only one way to tell that something was wrong, and that was that the arduino board wasn't able to launch an audio file and receive commands from the wemos. It had to be done in 2 steps, and it took me a long time to realize that the arduino board wasn't capable of doing both things at the same time, but that it had to be done in 2 steps, so I started programming a code to actually take the orders given by the wemos and then execute them, and not do both. But I know I've got some errors in my code that I'll have to go back to. 

After making progress but not finishing the part I wanted to do, because I'm still encountering problems that I'm going to sort out on Thursday I added the latest sensors, for the PIR Sensor I wrote a program that lets me enter the sensor manually because that part I can't manage automatically as for the sensor type. Incrementing the ID is done automatically. I used the same principle for my latest sensor, the photo resistance.

When I added a sensor, a device or data, I had to have a way of checking that what I'd added was actually in my database. So I had to create 3 recover files for my device, my sensors and of course my data. And since they have to be put in a JSON file, I just followed the instructions and put them in a JSON file.

I ended my day by writing programs that allowed me to delete a device, for example in my case the wemos, as I've modified my database so that when I delete the device, it automatically deletes the Sensor table and the SensorData if there's no longer a device in the table. The same goes for the Sensor, if I decide to delete a sensor it works normally, but if I no longer have a sensor in the table it deletes the SensorData table. And for the last table, if I need to delete a piece of data, there's no problem, even if I delete all the data in the table, it won't affect the other tables.

### Monday 10/03

Today I decided to go back to my embedded system and redo everything from scratch, I had to change my approach because I was missing some pins and my goal is to succeed in putting all the inputs on my wemos and all the outputs on my arduino board. Today I enlisted the help of Indigo, who gave me a lot of help with this part of the project. It took me the whole morning and afternoon to get it working. I started by connecting all my inputs, including my PIR sensor, the photoresistor and my button. Then I finished with my part with the various outputs. Which I did when I got home and did all my Frietzing part, which took me a long time, but tomorrow I'm going to keep working. I've set myself the goal of finishing all the embedded part today, all the connection part tomorrow, and after tomorrow all the data sending part between the wemos and my arduino board. 

---

## Fith week

## Friday 07/03

Today I went to see Mats to talk to him about my problems, what was too weird was when I put the local host to see the devices I had in my database. Before dealing with the loss of the connection, I wanted to make sure I could recover the device ids I'd already created, so I started by creating a recover device file that would allow me to just recover the devices I had in my database. I'd already created a device for the test device because I needed one to be able to add or delete appointments on my database. So after creating it, I did a “classic” test just by putting the link on the Internet and adding localhost without my IP address. I wanted to try again, the experience with my IP address where I had problems, I wanted to show my problems to Mats to show him my problems to my great surprise everything worked normally. I was really surprised and I was a man with more questions than before. I explained everything to Mats, from what I understood it was the fact that I was in my home network that was blocking my connection.
After the explanations I understood that I had to make a tunnel for it to work. Or use my phone's connection to make it work, but now I'll be able to go ahead and finish my embedded device part, my database part and send data to my database.

## Thursday 06/03

( Probably between 00h00 and 4h in the morning )
So I started by connecting all my first part which was to connect the easiest that is to say the LEDs to my wemos, although the LEDs do not send things to the wemos they can receive, my goal is to succeed in making when a person passes by that it can light.
The second component I connected was the button. I'd like to make it so that when someone presses it, it plays a game like my Dawn of War game, because anyone who's ever played that game knows how much the characters talk in it.
The PIR sensor to have a person detector to turn on the LEDs and play a sound when a person is in front of the smart calendar.
I wanted to connect my DF player but for some reason I'm having too many problems connecting it and I can't figure out why it's not working...

( 10h20 - 15h20 )
I started my day by wanting to continue to solve my DF Player mini problem but I'm still having problems. I wanted to restore my PIR sensor but for some reason it doesn't work anymore and I'm having the same problems as yesterday which is that it keeps showing me that a movement is detected when it's not.
I've connected the screen that allows me to display the heartbeat simulation to my arduous card.

(16h00 - 2h00)
As soon as I got home I set to work to make the best progress I could but for some reason my port 80 has a problem, I really don't know what to do to fix it I saw on the internet that you could change the port but being far from a pro I prefer to stop for today and ask Mats if he could give me a hand...

## Wenesday 05/03

Today I decided to work on the wemos connectivity part, I wanted to make myself a little schedule for the day to enable me to connect the wemos to my database, the first code I wrote allows me to retrieve the IP address of the wemos, I'll have to find a solution to manage to put it in a JSON file with its ID and IP address. 
I've found some videos explaining the different connections I could use, because I need to re-adapt the whole embedded device part for simplicity's sake, because putting all my sensors on the Wemos will enable me to access them more easily, whereas on the arduino board as I was planning to do, I could have encountered a lot of difficulties. So my goal for tonight is to redo the whole embedded device part, and if I make good and rapid progress I'll be able to finish it tonight. I don't know what time I'll go to bed, but in any case here's my plan for tonight.

## Tuesday 04/03

Today I spent the whole day dealing with one thing and that's connecting my website to my database, yesterday I'd managed to send an appointment to my database, the next step I had to take was to delete, modify and retrieve all the appointments in a JSON file. I started by learning about the API part, from what I found in the video a friend had given me. I needed an API for an “action”, so I created a delete, insert, update and recover. Then I saw in the assignments what was needed to have the above exceptation, so I spent the whole day doing that. To be able to display the add part correctly, for example, I had to create an API that would allow me to recover only the last appointment I'd added, by creating get_last_appointment.php with sceens shots. For proof of all this, I invite you to see my https://buudiizaaduu29-e0e00a.dev.hihva.nl/web/api_reference/. 
You'll be able to see everything I did for a whole day

## Monday 03/03

Today I've decided not to give up. Retreat is not an option! I started my day by reworking my data schema with the right conventions to redo the forward engineer and send it back to my database. I had a hard time understanding that I had to make all the attributes visible, but I admit I still don't understand why I had to do that.
Once my database was perfect, I took care of everything at once. In a youtube video, it was said that you had to create a php file for each major part of your code, i.e. what you wanted to do, e.g. if you wanted to add or delete an appointment, you had to create 2 and not put both in the same file. I created all the files I thought would be useful for my project, and the first thing I did was to add an appointment to my database. After 3 hours, I remembered that I'd set devide_id as a foreign key, and that if my device_id wasn't created, I couldn't add an appointment... It was a very sad moment
I manually created a test device with a random IP address with an SQL query to test my site, I was able to add one, then I added delete an appointment to be able to change it. 

---

## Fourth week

## Friday 28/02

### By the emperor it will be done ! 

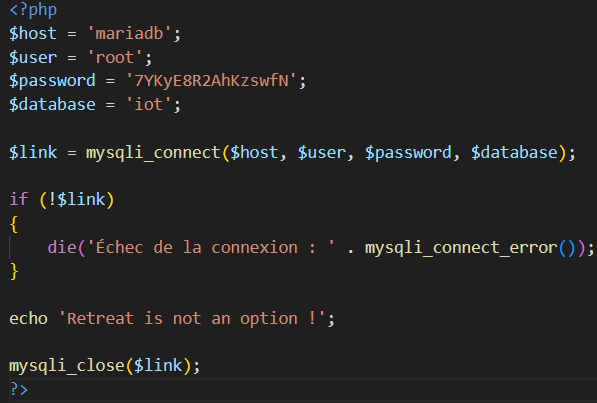
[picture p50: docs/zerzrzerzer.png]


truc

Finally, I succeeded (with the help of Yanis) my mistake was not to put the right name of the database, I spent so much time yesterday looking everywhere how to connect it. It was just the name, I want to smash everything !

## Thursday 27/02

Today I wasn't able to work on what I wanted to do, the teacher asked us to do a presentation on the front end, back end and database part. It's true that I learned a lot, but I must admit that I would have preferred to move on to what I really wanted to do, i.e. the connectivity part for my wemos and my website. It's really this part where I'm treading more on unfamiliar ground. Today I reread the feedback I'd received and saw that I had quite a few things to redo, which is what I did today. I had to redo my entire System architecture part, because the visibility wasn't up to scratch, and I also had to redo the text part because I'd missed some important information. As for the database part, it was Professor Mats (I hope I didn't misspell his first name...) who told us to be careful to justify our various choices, so I decided to take his advice and apply it to make it a priority. When my friend asked me what I thought of his requirement, he explained that it had to be well detailed so that if one day someone wanted to take over our project, he could deal with it easily. I went back to my requirement and completed it as best I could.

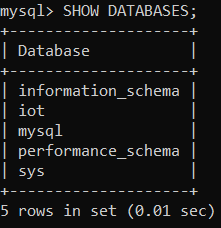
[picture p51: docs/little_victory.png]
victory


I've managed to access my database on my terminal, but I don't understand why I can't access it with my website. For some reason I'm completely stuck on this part, I don't know what to do even though I've watched the videos I wanted to see. I'm going to watch them again and ask for help with this part because I'm really struggling.

## Wednesday 26/02

Today I spoke to my teacher about my problems and he tried to help me. I still don't understand why I'm having these problems, but there's no question of withdrawing. I'm going to keep looking and finding a solution. I've tried changing all my cables, changing my speakers, changing the format of the audio files, changing the size of the files, I've tried everything and I don't know why I can't manage it, I'll try to sort it out next time maybe tomorrow or maybe not, I don't really know if I'm behind or if I'm on schedule with the project.
I decided to use a screen to display a simulated heartbeat to emphasize the machine-like aspect of my project. 
Unfortunately, the teacher didn't have a backpack to give me, so I wanted to connect the screen we'd been given to display the various tasks the user would be entering.
I wanted to go ahead and connect a 7-segment display to have a way of showing the time in real time, but I'm running out of space on my arduino board.
So instead I've decided to continue connecting my wires with a good “presentation” so that it's clearly visible, and I'm going to ask for feedback on this to see what they think. 
Today the teacher reminded us not to forget to add what we're doing on our System Architecture, so that's why I did it

## Tuesday 25/02

Today I really wanted to get my DFPlayer Mini working with my speakers, I finally managed to see about my resistors, thanks to my friends they helped me identify them properly because I have problems with some colors but with the right resistors I managed to get it working! I'm so happy that my DFPlayer Mini is working, I had a lot of problems with the “listing” part of my audio files. I had to rename them all, which took a bit of time, but I had no choice, because when I put in the 2nd audio file, it put me in the 20th. But now I'm running into a problem that I don't understand at all: when I change the file I'm compiling, it gives me saturations, whereas when I unplug and plug in my arduino board with the program already on it, it runs without saturation. I'm going to see the teacher tomorrow so he can give me a hand to understand all this

## Monday 24/02

Today I started my day early because my girlfriend is still here, she's leaving on Wednesday, which is why today I'm working in the morning as opposed to my habit of working late into the evening. This morning, someone in class had sent me a youtube link https://youtu.be/VnfX9YJbaU8?si=uhN22vAEtGgXQCOh I watched it to understand the whole connectivity part, I admit I have a lot of trouble with this part and it's the part that scares me the most...
While surfing the web I found the video I needed to learn how to connect my website to my database ! https://youtu.be/tHKsZdS8Oug?si=_tlX0Q8mqJxHsq8b
During the course I had my first lesson on the laser cutter, that we had programs that were already pre-made to help us, that we could customize infi because each line and each cut had its own parameter. That the cutting order was obviously important, and that we were even entitled to a board to help us set the right parameters for speed and distance. So I started thinking about how I was going to make my real final product. The laser cutter or the 3D printer, knowing that at our school we have 5 3D printers, and that I know I want to make something really in line with my theme, so I decided to go for the 3D printer, I did a lot of research to see what model I could use, and luckily found lots. There's a box I found that I'm going to use as a starting point and I'm going to change all the desuss elements to make a box that goes well with my theme.

---

## Third week ( Holiday )

## Thursday 20/02

Today was mainly the test phase, and although I was on vacation with my girlfriend, we took some time to work separately. For the construction part, I was disappointed to see that I'd made 2 very stupid mistakes concerning my LEDs: I'd reversed the anodes and catodes... I was able to run 2 test programs, one that lets me test my LEDs to see if everything's working properly, and the other my PIR sensor. In both cases, everything's working perfectly, so tomorrow I'll continue working on my real model and finally test my loudspeakers. 

## Tuesday 18/02

So today I didn't do much work because my girlfriend came to see me during the vacations, but today I really wanted to add my requirements section because I know that if I don't do it now I'll forget to do it. I sent my file with the audio files to her PC because for some reason my computer, which cost me over 1600 euros, doesn't have an SD drive, whereas hers does, so I sent her my audio files so she could put them on my SD card. And tomorrow I'm going to start assembling my components together and start coding on my arduino.

## Monday 17/02

I started my day by improving the layout of my cables to have a better view of my components and especially because I plan to add other components like a screen that I'll try to add tomorrow. I took care of my website to put a loading screen because my girlfriend had sent me a Tik Tok link to show me that there was a site that would allow me to add loading screens “easily”. The site is https://uiball.com/ldrs/.
But the problem with this site is that it took me at least 1h30 to reconfigure everything because the installation was a real pain to do. I wasted way too much time doing it. But now I'm happy, I've got a really nice site that I find really beautiful. I'll be asking for feedback next week. I tried to connect my website to my database but I lack the knowledge to do this part. I've tried everything I can but for some reason I just can't do it. But I'll keep checking tomorrow, I'll finally be able to start building my project, because last week I had to wait for my father to bring me the components I wanted and now I have to wait for my girlfriend to arrive because on her computer she has an SD card reader whereas on mine I don't have one.

---

## Second Week

## Friday 14/02
So today, I continued to work on the database part, I made some modifications that Mats had told me to make, I'm thinking particularly of the primary key, the indexes to foreign keys... I uploaded some files that weren't right, and improved some aspects of my planning. Oh yes, and I saw my mentor for the first time, or my coach, I forget which role he's affiliated with. I'm glad I managed to get Above Expectation, I imagine he was pleased with my work.

## Thursday 13/02
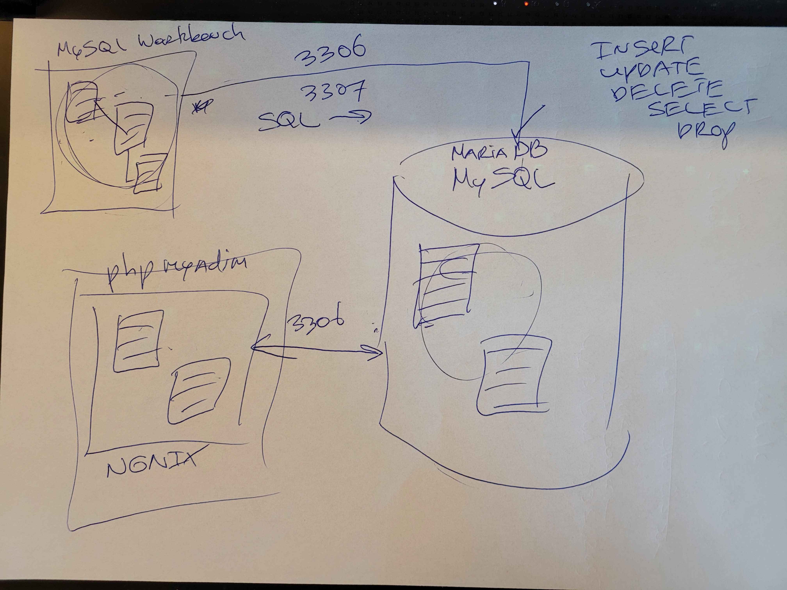
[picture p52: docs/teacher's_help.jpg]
Menu


I'd like to thank Professor Mats most of all, who more than helped me connect my mysql Workbrench to my database. I learned so many things at once and I'm happy because now I know how to do it and I know I could help my friends to solve this problem. First we need to connect with our account and that will give us the right ports and ip address. I didn't manage to do this last night, which is why I didn't stay up too late because I was blocked. Then the advantage I had was that all I had to do was retrieve my schema and with a few clicks (although I realised that I'd misconfigured my tables because you always have to reselect whether it's for the index, for foreign keys, etc.), I was able to create my own schema. And by doing all that, it works. Thanks again to Mats and Gerald (I hope I didn't misspell his first name) for helping me.

## Wednesday 12/02
  - Today I reread all my database courses because I'd completely forgotten how to represent entities with links. I learnt a new way of representing them with our teacher, who used to put ( 1, N ), well numbers and letters and not just bars. I've added some documentation because last night I didn't have time to do it, I've replaced an audio file that wasn't cut up properly, and I've finished my ERD diagram and the diagram for my database but I'm stuck and I don't understand why, I wanted to work a bit more but I'm limited...
  Today I reread all my database courses because I had completely forgotten how to represent entities with links. I learned a new way of representing them with our teacher who put ( 1, N ), finally numbers and letters and not only bars. I've added documentation because last night I didn't have time to do it, I've replaced a badly cut audio file, I've finished my ERD diagram and my database diagram but I'm stuck and I don't understand why, I wanted to work a bit harder but I'm limited... because I hadn't understood how to connect my SQL workbrench to my server that we had available. 

## Tuesday 11/02
  - Today I continued my model on Friztzing, I wanted to add the SG90 servo motor, although I haven't thought much about my final model I'm thinking of using it because I want to use the fact that this servo motor rotates to allow me to move my commissioner in and out. After finishing my model, I wanted to work on my first program, which would allow me to play an audio sound when the clock strikes a certain time, so I decided to cut out all the commissioner's voice lines so that I could use them, but I remembered that my father, who has the components, is coming to see me on Saturday, so I wanted to think about how I could send data to my wemos, but for some reason that I don't know about at school, the wemos wants to connect to the wifi, but when I'm at my apartment, it doesn't work at all. So I decided to take care of the front-end of my site, and that's what I did. And I'm proud of what I've done, I think my site's so beautiful! 
  - Last night I wanted to move forward on my website only the front end part to concentrate on the Data, API part because I have no idea how I'm going to manage to send the data from my website. I also wanted to do the diagram part to try and finish it, but being too tired I didn't manage to make as much progress as I'd hoped. As for the site, I've made pretty good progress, although of course there are things to improve, but I'll take care of those later. I hope I'm not wrong in saying that.

## Monday 10/02
  - Today I've learned to use Frietzing, I've learned to connect new components that I'd never used before. And I can't wait to continue making my circuits so that I can get to the programming phase. I know it's not going to be an easy thing to do, but it's going to be very interesting to be able to do it.

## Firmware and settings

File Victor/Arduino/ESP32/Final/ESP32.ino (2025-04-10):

/*
 Smart Calendar System for ESP32

  Author: Victor HOEGY
  Date: 2025-04
  MIT License
  copyright: (c) 2025, Victor HOEGY
  
 This program controls a smart calendar device with LCD display, 7-segment clock,
 DFPlayer for audio, servo motor, and various sensors. It connects to WiFi,
 fetches appointments from a server, and provides interactive features through
 physical buttons and web interface.

 */

 #include <Wire.h>
 #include <LiquidCrystal_I2C.h>
 #include <WiFiManager.h>
 #include <HTTPClient.h>
 #include <ArduinoJson.h>
 #include <DFRobotDFPlayerMini.h>
 #include <HardwareSerial.h>
 #include <NTPClient.h>
 #include <WiFiUdp.h>
 #include <TM1637Display.h>
 #include <WebServer.h>
 #include <ESP32Servo.h>

 // Hardware
 
// LCD
 const int LCD_I2C_ADDRESS = 0x27;     
 const int LCD_COLUMNS = 16;            
 const int LCD_ROWS = 2;               
 const int LCD_SDA_PIN = 21;           
 const int LCD_SCL_PIN = 22; 
 const int LCD_START_COL = 0;
 const int LCD_FIRST_LINE = 0;
 const int LCD_SECOND_LINE = 1;
           
 
// 7 segment 
 const int DISPLAY_CLK_PIN = 18;        
 const int DISPLAY_DIO_PIN = 19;         
 const uint8_t DISPLAY_BRIGHTNESS = 0x0a;
 const uint8_t DISPLAY_COLON_MASK = 0b01000000;
 const int DISPLAY_ERROR_CODE = 9999;   
 const int DISPLAY_DEFAULT_CODE = 8888; 
 const int DISPLAY_TIME_SCALING = 100; 
 
 // DFPlayer Mini 
 const int DFPLAYER_RX_PIN = 16;         
 const int DFPLAYER_TX_PIN = 17;         
 const int DFPLAYER_VOLUME = 15;          
 const int DFPLAYER_MIN_PLAY_INTERVAL_MS = 100;
 const int DFPLAYER_BAUD = 9600;        
 
 // Servo Motor 
 const int SERVO_PIN = 27;               
 const int SERVO_MIN_POSITION = 90;     
 const int SERVO_MAX_POSITION = 180;     
 const int SERVO_SPEED = 1;             
 const unsigned long SERVO_UPDATE_INTERVAL_MS = 20;
 const unsigned long SERVO_TEST_PAUSE_MS = 1000;    
 const unsigned long HOURLY_SERVO_DURATION_MS = 60000; 
 const int SERVO_PULSE_MIN = 500;      
 const int SERVO_PULSE_MAX = 2500;      
 const int SERVO_DIRECTION_FORWARD = 1;
 const int SERVO_DIRECTION_BACKWARD = -1;
 
 // Input 
 const int BUTTON_PIN = 14;             
 const int PIR_PIN = 35;                
 const int LDR_PIN = 34;          

 // Network    
 
 // NTP 
 const char* NTP_SERVER = "pool.ntp.org";
 const long NTP_UTC_OFFSET_SECONDS = 3600; 
 const char* DEFAULT_TIME_STRING = "1970-01-01 00:00:00";
 const size_t TIME_STRING_BUFFER_SIZE = 25;
 const char* TIME_STRING_FORMAT = "%Y-%m-%d %H:%M:%S"; 
 const int HOURS_PER_DAY = 24; 
 const int INVALID_HOUR = -1;

 
 // API 
 const char* APPOINTMENT_API_URL = "http://100.74.252.69/Database/Appointment/recover_appointment.php";
 const char* SENSOR_API_URL = "http://100.74.252.69/Database/SensorData/insert_sensor_data.php";
 
 // Server 
 const char* WIFI_AP_NAME = "SmartCalendarAP"; 
 const char* SERVER_ROOT_RESPONSE = "Smart Calendar is online!"; 
 const char* CONTENT_TYPE_TEXT = "text/plain"; 
 const char* CONTENT_TYPE_JSON = "application/json"; 
 const int HTTP_OK_CODE = 200;           
 const int HTTP_SERVICE_UNAVAILABLE_CODE = 503; 

 const size_t APPOINTMENT_JSON_DOC_SIZE = 2048;
 
 // Serial monitor
 const int SERIAL_BAUD = 115200;        

 // ID
 
 const int DEVICE_ID = 1; // ESP32's ID
 
 enum SensorIds 
 {
   BUTTON_SENSOR_ID = 1, 
   PIR_SENSOR_ID = 2,        
   LDR_SENSOR_ID = 3           
 };
 
 // Timing
 const unsigned long APPOINTMENT_REFRESH_INTERVAL_MS = 5000; 
 const unsigned long DISPLAY_INTERVAL_MS = 3000;    
 const unsigned long SENSOR_CHECK_INTERVAL_MS = 50; 
 const unsigned long TIME_UPDATE_INTERVAL_MS = 60000; 
 const unsigned long NTP_RETRY_INTERVAL_MS = 30000; 
 const unsigned long BUTTON_DEBOUNCE_TIME_MS = 50;  
 const unsigned long WIFI_RECONNECT_DELAY_MS = 1000; 
 const unsigned long DELAY_WIFI_FAIL_MS = 3000;    
 const unsigned long DELAY_AFTER_RESTART_MS = 5000; 
 const unsigned long CHARACTER_NOTIFICATION_DURATION_MS = 2000; 
 const unsigned long PIR_INTERVAL_MS = 300000;     
 const unsigned long WIFI_TIMEOUT_MS = 30000;     
 const unsigned long WATCHDOG_INTERVAL_MS = 60000; 
 const unsigned long MAX_UPTIME_MS = 86400000;  
 const int TIMEZONE_OFFSET_HOURS = 1;
 
 // Night Mode
 const int NIGHT_MODE_ENTER_THRESHOLD = 650; 
 const int NIGHT_MODE_EXIT_THRESHOLD = 750;  
 
 // Character Modes 
 enum CharacterMode 
 { 
   COMMISSAR,                       
   LEMAN_RUSS,                      
   BANEBLADE,                      
   CHARACTER_MODE_COUNT             
 };

 const int CHARACTER_CYCLE_STEP = 1;

 const int APPOINTMENT_CYCLE_STEP = 1;

 
 // Servo Test 
 const int INITIAL_PHASE = 0;        
 const int PAUSE_PHASE = 1;        
 const int RETURN_PHASE = 2;         

 // TRUE FALSE
 const int VALUE_TRUE = 1;           
 const int VALUE_FALSE = 0;         
 
 // Date 
 const int DATE_STRING_LENGTH_THRESHOLD = 16; 
 const int INDEX_DAY_START = 8;      
 const int INDEX_DAY_END = 10;      
 const int INDEX_MONTH_START = 5;  
 const int INDEX_MONTH_END = 7;      
 const int INDEX_TIME_START = 11;   
 const int INDEX_TIME_END = 16;      
 
 // Message
 
 // LCD Message 
 const char* LCD_MSG_INIT = "Initializing...";
 const char* LCD_MSG_TEST_SERVO = "Testing servo...";
 const char* LCD_MSG_NO_APPOINTMENTS = "No appointments";
 const char* LCD_MSG_INVALID_DATE = "Invalid date";
 const char* LCD_MSG_TIME_INIT = "Time initialized";
 const char* LCD_MSG_TIME_FAIL = "Time init failed";
 const char* LCD_MSG_FETCHING = "Fetching data...";
 const char* LCD_MSG_RETRYING = "Retrying...";
 const char* LCD_MSG_WIFI_START = "Starting WiFi";
 const char* LCD_MSG_WIFI_FAIL = "WiFi Failed";
 const char* LCD_MSG_WIFI_CONNECTED = "WiFi Connected";
 const char* LCD_MSG_SYNCING = "Syncing time...";
 const char* LCD_MSG_RESTARTING = "Restarting...";
 const char* LCD_MSG_FETCH_FAIL = "Fetch failed";
 const char* LCD_MSG_SWITCHED = "Switched to";
 
 // Serial Monitor Message
 const char* SERIAL_MSG_TIME_INIT = "Time initialized";
 const char* SERIAL_MSG_TIME_FAIL = "Time init failed";
 const char* SERIAL_MSG_TEST_SERVO = "Testing servo: max -> min -> pause -> max";
 const char* SERIAL_MSG_SERVO_FAIL = "Failed to attach servo!";
 const char* SERIAL_MSG_SERVO_ATTACHED = "Servo attached";
 const char* SERIAL_MSG_SERVO_TEST_COMPLETE = "Servo test complete";
 const char* SERIAL_MSG_DFPLAYER_INIT = "DFPlayer initialized";
 const char* SERIAL_MSG_DFPLAYER_FAIL = "DFPlayer initialization failed!";
 const char* SERIAL_MSG_SERVO_MOVING_MIN = "Servo moving slowly to minimum position";
 const char* SERIAL_MSG_SERVO_MOVING_MAX = "Servo returning slowly to maximum position";
 const char* SERIAL_MSG_SERVO_REACHED = "Servo reached target position";
 const char* SERIAL_MSG_WIFI_TIMEOUT = "WiFi connection timeout, continuing offline";
 const char* SERIAL_MSG_HTTP_STARTED = "HTTP server started";
 const char* SERIAL_MSG_IP_ADDRESS = "IP address: ";
 
 // Web Server Responses 
 const char* SERVER_SWITCH_RESPONSE = "Character changed to ";
 
// Variables
 LiquidCrystal_I2C lcd(LCD_I2C_ADDRESS, LCD_COLUMNS, LCD_ROWS);
 TM1637Display display(DISPLAY_CLK_PIN, DISPLAY_DIO_PIN);
 WiFiUDP ntpUDP;
 WebServer server(80);
 NTPClient timeClient(ntpUDP, NTP_SERVER, NTP_UTC_OFFSET_SECONDS);
 HardwareSerial mySoftwareSerial(2);
 DFRobotDFPlayerMini dfPlayer;
 Servo servo1;
 
 CharacterMode currentCharacter = COMMISSAR; 
 String currentCharacterNames[CHARACTER_MODE_COUNT] = 
 {
   "Commissar",                 
   "Leman Russ",                
   "Baneblade"                  
 };
 
 DynamicJsonDocument appointments(APPOINTMENT_JSON_DOC_SIZE);    
 std::vector<String> previousAppointmentIds; 
 
 // Timing Trackers 
 unsigned long lastAppointmentRefresh = 0;  
 unsigned long lastDisplayChange = 0;       
 unsigned long lastSensorCheck = 0;         
 unsigned long lastTimeUpdate = 0;          
 unsigned long lastNtpRetry = 0;           
 unsigned long lastButtonPress = 0;        
 unsigned long lastReconnectAttempt = 0;    
 unsigned long lastHourCheck = 0;           
 unsigned long characterNotificationStart = 0; 
 unsigned long lastPIRTime = 0;           
 
 // State Trackers 
 int currentAppointmentIndex = 0;     
 int lastButtonState = HIGH;               
 int lastPIRState = LOW;                    
 int lastLDRValue = -1;                   
 
 bool timeInitialized = false;              
 bool dfPlayerInitialized = false;         
 bool dataRefreshed = false;                
 bool nightMode = false;                   
 bool showingCharacterNotification = false; 
 bool pirLocked = false;                   
 
 // Servo Control 
 int servoCurrentPosition = SERVO_MAX_POSITION; 
 int servoTargetPosition = SERVO_MAX_POSITION; 
 unsigned long lastServoUpdate = 0;         
 unsigned long servoReturnTime = 0;        
 bool servoMoving = false;                 
 
// Sound
 const int COMMISSAR_TRACK = 31;            
 const int LEMAN_RUSS_TRACK = 42;          
 const int BANEBLADE_TRACK = 53;          
 const int DARK_TRACK = 35;                
 const int LIGHT_TRACK = 36;              
 const int COMMISSAR_ACTIVE_TRACKS[] = {1,2,3,4,5,6,7,8,9,10,12,13,14,15,16,17,18,19,21,22,28,33,34};
 const int COMMISSAR_DELETED_TRACKS[] = {11,20,23,24,25,26,27,29,30,32};
 const int LEMAN_RUSS_ACTIVE_TRACKS[] = {43,44,45,46,47,48};
 const int LEMAN_RUSS_DELETED_TRACKS[] = {49,50,51};
 const int BANEBLADE_ACTIVE_TRACKS[] = {52,53,54,55,56,57,58,59,60,61,62,63,67,68,69,70,71,72,73,74};
 const int BANEBLADE_DELETED_TRACKS[] = {64,65,66};
 const int PIR_TRACKS[] = {37,38,39,40,41}; 
 
 // Display States 
 enum DisplayState 
 {
   SHOWING_CHARACTER_NOTIFICATION,   
   SHOWING_APPOINTMENTS,             
   SHOWING_NO_APPOINTMENTS,         
   SHOWING_INITIALIZATION            
 };
 DisplayState currentDisplayState = SHOWING_INITIALIZATION; 
 
// Updates the LCD display with new content if it has changed
 void updateDisplay(String line1, String line2, DisplayState newState) 
 {
   static String lastLine1 = "";      // Previously displayed first line
   static String lastLine2 = "";      // Previously displayed second line
   static DisplayState lastState = SHOWING_INITIALIZATION; // Previous state
 
   // Only update display if content or state has changed
   if (newState != lastState || line1 != lastLine1 || line2 != lastLine2) 
   {
     lcd.clear();  // Clear the display before showing new content
     
     // Display first line
     lcd.setCursor(LCD_START_COL, LCD_FIRST_LINE);
     lcd.print(line1.substring(0, LCD_COLUMNS));
 
     // Display second line
     lcd.setCursor(LCD_START_COL, LCD_SECOND_LINE);
     lcd.print(line2.substring(0, LCD_COLUMNS));
 
     // Update tracking variables
     lastLine1 = line1;
     lastLine2 = line2;
     lastState = newState;
     currentDisplayState = newState;
   }
 }
 
// Updates the 7-segment display with current time
 void update7SegmentDisplay() 
 {
   // Show error code if time hasn't been initialized
   if (!timeInitialized) 
   {
     display.showNumberDec(DISPLAY_ERROR_CODE);
     return;
   }
   
   // Update time from NTP server and display it
   timeClient.update();
   int hour = timeClient.getHours() + TIMEZONE_OFFSET_HOURS; // Adjust for timezone
   // Handle 24-hour rollover
   if (hour >= HOURS_PER_DAY) hour -= HOURS_PER_DAY;
   int minute = timeClient.getMinutes();
   // Display time with colon (e.g., 12:34)
   int timeDisplay = hour * DISPLAY_TIME_SCALING + minute;
   display.showNumberDecEx(timeDisplay, DISPLAY_COLON_MASK, true);
 }
 
// Initializes time synchronization with NTP server
 void initializeTime() 
 {
   // Attempt to force an NTP time update
   if (timeClient.forceUpdate()) 
   {
     timeInitialized = true;
     Serial.println(SERIAL_MSG_TIME_INIT);
     updateDisplay(LCD_MSG_TIME_INIT, LCD_MSG_FETCHING, SHOWING_INITIALIZATION);
   } 
   
   else 
   {
     Serial.println(SERIAL_MSG_TIME_FAIL);
     updateDisplay(LCD_MSG_TIME_FAIL, LCD_MSG_RETRYING, SHOWING_INITIALIZATION);
   }
 }
 
// Connects to WiFi using WiFiManager
 void connectToWiFi() 
 {
   WiFiManager wifiManager;
   updateDisplay(LCD_MSG_WIFI_START, "", SHOWING_INITIALIZATION);
   
   // Attempt to connect to WiFi or start configuration AP
   if (!wifiManager.autoConnect(WIFI_AP_NAME)) 
   {
     // Connection failed show message and restart
     updateDisplay(LCD_MSG_WIFI_FAIL, LCD_MSG_RESTARTING, SHOWING_INITIALIZATION);
     delay(DELAY_WIFI_FAIL_MS);
     ESP.restart();
     delay(DELAY_AFTER_RESTART_MS);
   }
   
   // Connection successful proceed to time sync
   updateDisplay(LCD_MSG_WIFI_CONNECTED, LCD_MSG_SYNCING, SHOWING_INITIALIZATION);
   initializeTime();
 }
 
// Fetches appointments from the API server
 void fetchAppointments() 
 {
   HTTPClient http;
   http.begin(APPOINTMENT_API_URL);
 
   // Make GET request to appointment API
   int httpCode = http.GET();
   
   // Process response if successful
   if (httpCode == HTTP_CODE_OK) 
   {
     String payload = http.getString();
     DynamicJsonDocument newAppointments(APPOINTMENT_JSON_DOC_SIZE);
     deserializeJson(newAppointments, payload);
     checkForAppointmentChanges(newAppointments);
   } 
   
   else 
   {
     // Show error if fetch failed
     updateDisplay(LCD_MSG_FETCH_FAIL, LCD_MSG_RETRYING, SHOWING_INITIALIZATION);
   }
 
   http.end(); // Free resources
 }
 
// Compares new appointments with previous ones and triggers appropriate actions
 void checkForAppointmentChanges(DynamicJsonDocument& newAppointments) 
 {
   std::vector<String> currentIds;    // Track IDs of current appointments
   bool changesDetected = false;      // Flag for any detected changes
 
   // Check for new or modified appointments
   for (JsonObject newApp : newAppointments.as<JsonArray>()) 
   {
     String newAppId = newApp["appointment_id"].as<String>();
     currentIds.push_back(newAppId);
 
     bool isNew = true;
     bool isModified = false;
     
     // Compare with previous appointments
     for (String prevId : previousAppointmentIds) 
     {
       if (prevId == newAppId) 
       {
         isNew = false;
 
         // Check if existing appointment has changed
         for (JsonObject oldApp : appointments.as<JsonArray>()) 
         {
           if (oldApp["appointment_id"].as<String>() == newAppId) 
           {
             if (oldApp["task"] != newApp["task"] || oldApp["date_hour"] != newApp["date_hour"]) {
               isModified = true;
             }

             break;
           }
         }

         break;
       }
     }
 
     // Play sound for new or modified appointments (unless in night mode)
     if ((isNew || isModified) && !nightMode) 
     {
        playAppropriateSound(VALUE_TRUE);
        changesDetected = true;
     }
   }
 
   // Check for deleted appointments
   for (String prevId : previousAppointmentIds) 
   {
     bool stillExists = false;
     for (JsonObject newApp : newAppointments.as<JsonArray>()) 
     {
       if (newApp["appointment_id"].as<String>() == prevId) 
       {
          stillExists = true;
          break;
       }
     }
 
     // Play sound for deleted appointments (unless in night mode)
     if (!stillExists && !nightMode) 
     {
       playAppropriateSound(VALUE_FALSE);
       changesDetected = true;
     }
   }
 
   // Update stored appointments if changes detected or first load
   if (changesDetected || previousAppointmentIds.empty()) 
   {
     appointments = newAppointments;
     previousAppointmentIds = currentIds;
     currentAppointmentIndex = 0;
     lastDisplayChange = millis();
   }
 }
 
// Plays an appropriate sound based on current character mode and event type
 void playAppropriateSound(bool isActiveOrUpdated) 
 {
   // Don't play sounds if DFPlayer isn't ready or in night mode
   if (!dfPlayerInitialized || nightMode) return;
   
   // Select sound set based on current character mode
   switch(currentCharacter) 
   {
     case COMMISSAR:
       playRandomSound(isActiveOrUpdated ? COMMISSAR_ACTIVE_TRACKS : COMMISSAR_DELETED_TRACKS, 
                     isActiveOrUpdated ? sizeof(COMMISSAR_ACTIVE_TRACKS)/sizeof(int) : 
                                       sizeof(COMMISSAR_DELETED_TRACKS)/sizeof(int));
       break;
     case LEMAN_RUSS:
       playRandomSound(isActiveOrUpdated ? LEMAN_RUSS_ACTIVE_TRACKS : LEMAN_RUSS_DELETED_TRACKS,
                     isActiveOrUpdated ? sizeof(LEMAN_RUSS_ACTIVE_TRACKS)/sizeof(int) : 
                                       sizeof(LEMAN_RUSS_DELETED_TRACKS)/sizeof(int));
       break;
     case BANEBLADE:
       playRandomSound(isActiveOrUpdated ? BANEBLADE_ACTIVE_TRACKS : BANEBLADE_DELETED_TRACKS,
                     isActiveOrUpdated ? sizeof(BANEBLADE_ACTIVE_TRACKS)/sizeof(int) : 
                                       sizeof(BANEBLADE_DELETED_TRACKS)/sizeof(int));
       break;
   }
 }
 
// Displays the current appointment on the LCD
 void displayCurrentAppointment(unsigned long currentMillis) 
 {
   // Don't update display if showing character notification
   if (showingCharacterNotification) return;
   
   // Show "no appointments" message if none are available
   if (appointments.size() == 0) 
   {
     if (currentDisplayState != SHOWING_NO_APPOINTMENTS) 
     {
       updateDisplay(LCD_MSG_NO_APPOINTMENTS, "", SHOWING_NO_APPOINTMENTS);
     }

     return;
   }
 
   // Rotate to next appointment at defined interval
   if (currentMillis - lastDisplayChange >= DISPLAY_INTERVAL_MS) 
   {
     currentAppointmentIndex = (currentAppointmentIndex + APPOINTMENT_CYCLE_STEP) % appointments.size();
     lastDisplayChange = currentMillis;
   }
 
   // Get current appointment data
   JsonObject appointment = appointments[currentAppointmentIndex];
   String task = appointment["task"].as<String>();
   String dateTime = appointment["date_hour"].as<String>();
 
   // Format date string (DD/MM HH:MM)
   String line2 = "";
   if (dateTime.length() >= DATE_STRING_LENGTH_THRESHOLD) 
   {
     line2 = dateTime.substring(INDEX_DAY_START, INDEX_DAY_END) + "/" + 
             dateTime.substring(INDEX_MONTH_START, INDEX_MONTH_END) + " " + 
             dateTime.substring(INDEX_TIME_START, INDEX_TIME_END);
   } 
   
   else 
   {
     line2 = LCD_MSG_INVALID_DATE;
   }
 
   // Truncate task if too long for display
   if (task.length() > LCD_COLUMNS) 
   {
     task = task.substring(0, LCD_COLUMNS);
   }
 
   // Update display with appointment info
   updateDisplay(task, line2, SHOWING_APPOINTMENTS);
 }
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
 void loop() 
 {
   unsigned long currentMillis = millis();
 
   // Handle any incoming web server requests
   server.handleClient();
 
   // Manage WiFi connection state with timeout
   static unsigned long wifiTimeout = 0;
   if (WiFi.status() != WL_CONNECTED) 
   {
     // Attempt to reconnect if delay period has passed
     if (currentMillis - lastReconnectAttempt >= WIFI_RECONNECT_DELAY_MS) 
     {
       // Initialize timeout on first attempt
       if (wifiTimeout == 0) wifiTimeout = currentMillis + WIFI_TIMEOUT_MS; 
       
       // Only try to reconnect if within timeout window
       if (currentMillis < wifiTimeout) {
         lastReconnectAttempt = currentMillis;
         connectToWiFi();
       } 
       
       else 
       {
         // Continue operation offline after timeout
         Serial.println(SERIAL_MSG_WIFI_TIMEOUT);
         wifiTimeout = 0;
       }
     }
   } 
   
   else 
   {
     // Reset timeout when connected
     wifiTimeout = 0;
   }
 
   // Update 7-segment display clock at regular interval
   if (currentMillis - lastTimeUpdate >= TIME_UPDATE_INTERVAL_MS) 
   {
     if (timeInitialized) 
     {
       update7SegmentDisplay();
     }

     lastTimeUpdate = currentMillis;
   }
 
   // Retry NTP time synchronization if not yet initialized
   if (!timeInitialized && currentMillis - lastNtpRetry >= NTP_RETRY_INTERVAL_MS) 
   {
     initializeTime();
     lastNtpRetry = currentMillis;
   }
 
   // Refresh appointment data if needed
   if (!dataRefreshed) 
   {
     fetchAppointments();
     dataRefreshed = true;
     lastAppointmentRefresh = currentMillis;
   }
 
   // Mark data as needing refresh when interval elapses
   if (currentMillis - lastAppointmentRefresh >= APPOINTMENT_REFRESH_INTERVAL_MS) 
   {
     dataRefreshed = false;
   }
 
   // Update display with current appointment
   displayCurrentAppointment(currentMillis);
   
   // Process all sensor inputs
   handleSensors(currentMillis);
   
   // Handle hourly servo movement (visual clock function)
   handleHourlyServo(currentMillis);
 
   // Clear character notification after display duration
   if (showingCharacterNotification && currentMillis - characterNotificationStart >= CHARACTER_NOTIFICATION_DURATION_MS) 
    {
      showingCharacterNotification = false;
      currentDisplayState = SHOWING_APPOINTMENTS;
      lastDisplayChange = 0;
    }
 
   // Watchdog timer to restart after maximum uptime
   static unsigned long lastWatchdogCheck = 0;
   if (currentMillis - lastWatchdogCheck >= WATCHDOG_INTERVAL_MS) 
   { 
     lastWatchdogCheck = currentMillis;
     if (millis() > MAX_UPTIME_MS) 
     { 
       ESP.restart(); 
     }
   }
 }

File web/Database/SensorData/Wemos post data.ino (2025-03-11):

#include <ESP8266WiFi.h>
#include <ESP8266HTTPClient.h>

#define BOUTON_PIN 16 
#define PIR_SENSOR_PIN D2 
#define LDR_PIN A0

const char* ssid = "DeKey-Fraijlemaborg";
const char* password = "i3xHp*ag";

const char* apiUrl = "http://100.74.252.69/Database/SensorData/insert_sensor_data.php";

WiFiClient wifiClient;

int lastButtonState = HIGH;
int lastPIRState = LOW;
int lastLDRState = -1;
unsigned long lastPIRTime = 0;
bool pirLocked = false;
const long pirInterval = 300000;

void setup() {
    Serial.begin(115200);
    WiFi.begin(ssid, password);

    Serial.print("Connexion au Wi-Fi...");
    while (WiFi.status() != WL_CONNECTED) 
    {
        delay(500);
        Serial.print(".");
    }

    Serial.println("\nConnecté au Wi-Fi.");
    Serial.print("IP: ");
    Serial.println(WiFi.localIP());

    pinMode(BOUTON_PIN, INPUT_PULLUP);
    pinMode(PIR_SENSOR_PIN, INPUT);
}

void sendSensorData(int sensor1, float value1, int sensor2, float value2, int sensor3, float value3) 
{
    if (WiFi.status() == WL_CONNECTED) 
    {
        HTTPClient http;

        String postData = "sensor_id_1=" + String(sensor1) + "&value_1=" + String(value1) +
                          "&sensor_id_2=" + String(sensor2) + "&value_2=" + String(value2) +
                          "&sensor_id_3=" + String(sensor3) + "&value_3=" + String(value3);

        Serial.println("📡 Envoi des données : " + postData);

        http.begin(wifiClient, apiUrl);
        http.addHeader("Content-Type", "application/x-www-form-urlencoded");

        int httpResponseCode = http.POST(postData);

        if (httpResponseCode > 0) 
        {
            String response = http.getString();
            Serial.println("📡 Réponse du serveur : ");
            Serial.println(response);
        } 
        
        else 
        {
            Serial.print("❌ Erreur HTTP : ");
            Serial.println(httpResponseCode);
        }

        http.end();
    } 
    
    else 
    {
        Serial.println("❌ WiFi déconnecté, tentative de reconnexion...");
    }
}

void loop() 
{
    int buttonState = digitalRead(BOUTON_PIN);
    int pirState = digitalRead(PIR_SENSOR_PIN);
    int ldrValue = analogRead(LDR_PIN);

    if (buttonState == LOW && lastButtonState == HIGH) 
    {
        Serial.println("🔘 Bouton pressé ! Envoi des données...");
        sendSensorData(1, 1, 2, pirState, 3, ldrValue);
    }
    lastButtonState = buttonState;

    if (pirState == HIGH && lastPIRState == LOW && !pirLocked) 
    {
        Serial.println("🚨 Mouvement détecté ! Envoi immédiat...");
        sendSensorData(1, buttonState == LOW ? 1 : 0, 2, pirState, 3, ldrValue);
        lastPIRTime = millis(); 
        pirLocked = true;  
    }

    if (pirLocked && millis() - lastPIRTime >= pirInterval) 
    {
        Serial.println("🔓 PIR débloqué, prêt pour une nouvelle détection !");
        pirLocked = false;
    }

    lastPIRState = pirState;

    int currentLDRState = (ldrValue < 200) ? 0 : 1;

    if (currentLDRState != lastLDRState) 
    {
        Serial.print("🔆 Changement de luminosité détecté ! Nouvelle valeur : ");
        Serial.println(ldrValue);
        sendSensorData(1, buttonState == LOW ? 1 : 0, 2, pirState, 3, ldrValue);
        lastLDRState = currentLDRState;
    }

    delay(50);
}

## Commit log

2025-02-07 Tableau créer pour de bon
2025-02-10 Le détail de mon blueprint
2025-02-10 Create a circuit validate on the planning
2025-02-10 Upload New File
    [circuit_Arduino_DFPlayer_ESP8266_PIR_sensor.fzz]
2025-02-10 Replace circuit_Arduino_DFPlayer_ESP8266_PIR_sensor.png
2025-02-12 Add appointment button below text
2025-02-17 Adding new arduino better wire management
2025-02-17 Importation screen chargement
2025-02-17 Charging screen add and add css file
2025-02-17 Reajustment for the charging screen
2025-02-20 LED test program
2025-02-20 PIR sensor test programme
2025-02-24 Astra militarum Emblem1
    [Astra Militarum Emblem1.stl]
2025-02-24 Astra Militarum Emblem
    [Astra Militarum Emblem2.stl, Astra Militarum Emblem3.stl, Astra Militarum Emblem4.stl]
2025-02-24 Box add
    [Column_peg.stl, Top_brace.stl, Top_flat_brace.stl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]
2025-02-25 Add voice lines with good rename for arduino
2025-02-26 Replace circuit_Arduino_DFPlayer_ESP8266_PIR_sensor_speaker_motor_final_I_hope.png
2025-02-27 Embedded file devide
    [Embedded device.fzz]
2025-02-27 Table sensor
2025-02-28 Last before bed
2025-02-28 Color wire changed better view
2025-03-03 edit button website
2025-03-03 show auto charging appointment
2025-03-03 Insert appointment working
2025-03-04 API insert
2025-03-04 Insert upload
2025-03-04 Insert appointment upload API
2025-03-05 Embedded device construction part
2025-03-05 Button code
2025-03-05 LED upload
2025-03-05 LED Check
2025-03-05 Photo resistor + Planning
2025-03-06 Button upload wemos
2025-03-06 PIR sensor done
2025-03-06 ✅ Heartbeat -> Arduino
2025-03-06 Servo motor arduino
2025-03-06 LED Upload for save some pins on the wemos
2025-03-06 Insert device
2025-03-06 JSON file recover device
2025-03-06 wemos post device
2025-03-07 Port 80 problem, completely blocked
    [Wemos post device.ino]
2025-03-09 PIR sensor working now !
2025-03-10 Arduino code com wemos
2025-03-10 Wemos code com arduino
2025-03-11 Insert upload check if ip adress is here or not
2025-03-11 insert sensor database
2025-03-11 Check if same names sensor
2025-03-11 insert sensor data button
2025-03-11 Change pin
2025-03-11 arduino connected to the wemos for the DF Player Mini
2025-03-11 Wemos connected to the arduino to play a sound when someone hit the button
2025-03-11 recover sensor
2025-03-11 Insert sensor data
2025-03-11 Recover sensor data
2025-03-11 Insert sensor upload
2025-03-12 Technical documentation embedded device need to improve it
2025-03-12 Embedded device changements after feedback
2025-03-12 Circuits upload
    [Embedded device.fzz, circuit_Arduino_DFPlayer_ESP8266_PIR_sensor.fzz]
2025-03-12 Technical documentation embedded device
2025-03-13 Didn't work the code for the Wemos to the Arduino need to fix it in few hours need to sleep
2025-03-17 Button connected to the ESP32
2025-03-17 Photo resistor connected to the wemos
2025-03-17 DF Player Mini connected ESP32
2025-03-17 DF Player mini with Button
2025-03-17 Led connected to the ESP32
2025-03-17 7 segments connected to the ESP32
2025-03-17 Both screen connected to the ESP32
2025-03-17 Servo connected to the ESP32
2025-03-17 Add note for insert appointment
2025-03-18 Code on the eSP32 who can able to retrieve the appointents display them and play a sound according to the added notes ( need to fix this )
2025-03-18 ESP32 upload
2025-03-18 Button, DF Player and 2 Screens working
2025-03-20 Step 1 stl file
    [Step1.stl]
2025-03-20 Step 4
    [Step2.stl, Step4.stl]
2025-03-20 Step6 upload
    [Step4.stl, Step6.stl]
2025-03-20 Step 7 & 8
    [Step8.stl]
2025-03-24 Step 9
    [Step9.stl]
2025-03-24 Step 10 Upload
    [Step10.stl]
2025-03-24 Step 18
    [Step18.stl]
2025-03-24 ESP32 code
2025-03-24 Sensor to the database from the ESP32
2025-03-25 PIR sensor voice lines
2025-03-25 Step 19
    [Step19.stl]
2025-03-26 Last one
    [Cuckoo.stl, Last.stl, Step222.stl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]
2025-03-26 Embedded device upload
    [Embedded device.fzz]
2025-04-03 Research part upload
    [Astra_Militarum_Explication.stl]
2025-04-08 ESP32 Update
